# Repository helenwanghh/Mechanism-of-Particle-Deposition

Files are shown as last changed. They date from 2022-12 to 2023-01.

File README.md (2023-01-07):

# Mechanism-of-Particle-Deposition
Hello there!  Here is a project portfolio for my Senior Capstone Project (2021-2022)
This is a project provided by **Integrity Industrial Inkjet Integration** who needed a printing manufacturing process that can print on a wide range of surfaces. 

Please click the link to check out the Users Operation Instrution Video: 
Instruction Video for the Mechanism Design (https://www.youtube.com/embed/nuajtc9fk5U)
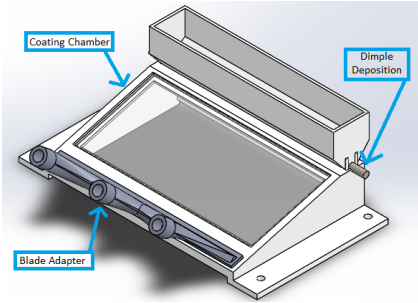
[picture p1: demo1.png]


- **Background**

The client currently has a method of layering adhesive and various powders on an inkjet conveyor that does not meet their standards.

- **Problem**

Provide proof of principle, using glitter as a substitute for various powders. The module is to be attached to a conveyor belt along with an Inkjet printer head that will dispense a uniform coating of glitter on an adhesive with a method to recover and reuse any additional glitter that is not used.

- **Benefits**

A fully functional module will prevent material waste and reduce cost while producing high quality/ high resolution prints for clients across several industries.

 **Client Requirements**

- Maintain clean workspace and ensure  minimal glitter escapes the box 
- Maximize glitter use to create less waste and reduce cost on materials
- A way to easily control device to stop or divert the glitter flow
- Must only remove excess glitter and not glitter that has been adhered
- Be able to do multiple colors of glitters and multiple layers of glute/glitters
- Must not exceed surface area of conveyer belt plate: 7.5'' x 7.5''

**Team picture captured at the Design Night at University of Vermont!! :) **
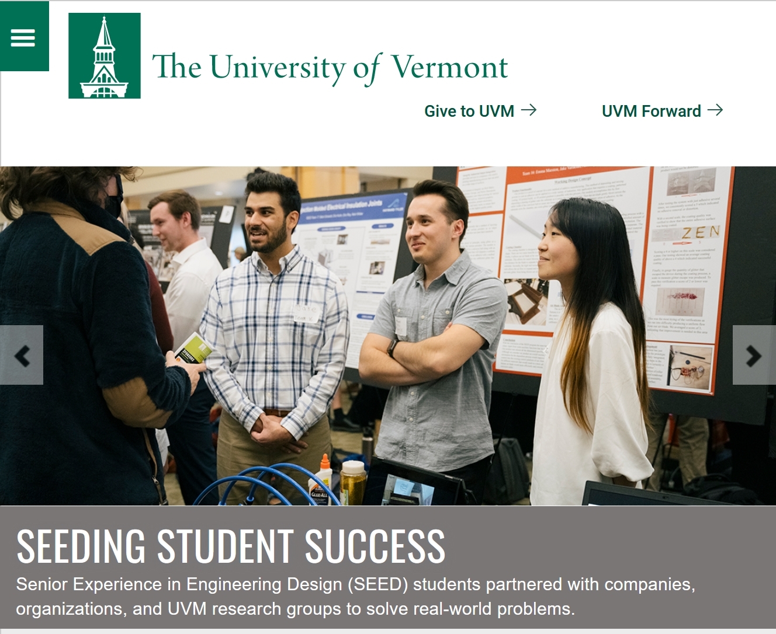
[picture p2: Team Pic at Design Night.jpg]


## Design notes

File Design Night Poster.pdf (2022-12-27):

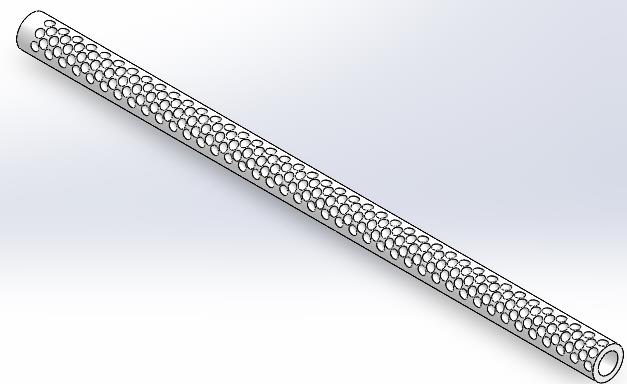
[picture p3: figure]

Background

The client currently has a method of layering adhesive and various powders on an inkjet conveyor that does not meet their standards.

Problem

Provide proof of principle, using glitter as a substitute for various powders. The module is to be attached to a conveyor belt along with an Inkjet printer head that will dispense a uniform coating of glitter on an adhesive with a method to recover and reuse any additional glitter that is not used.

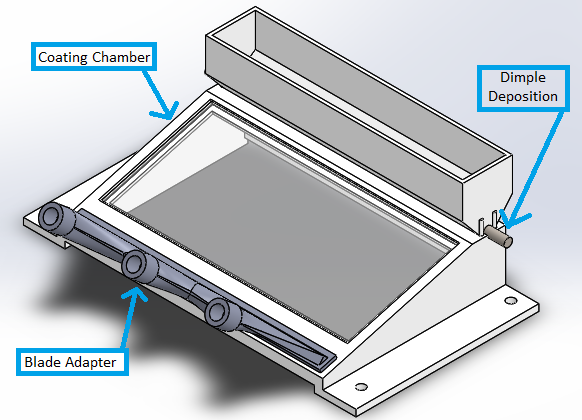
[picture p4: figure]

Benefits

A fully functional module will prevent material waste and reduce cost while producing high quality/ high resolution prints for clients across several industries.

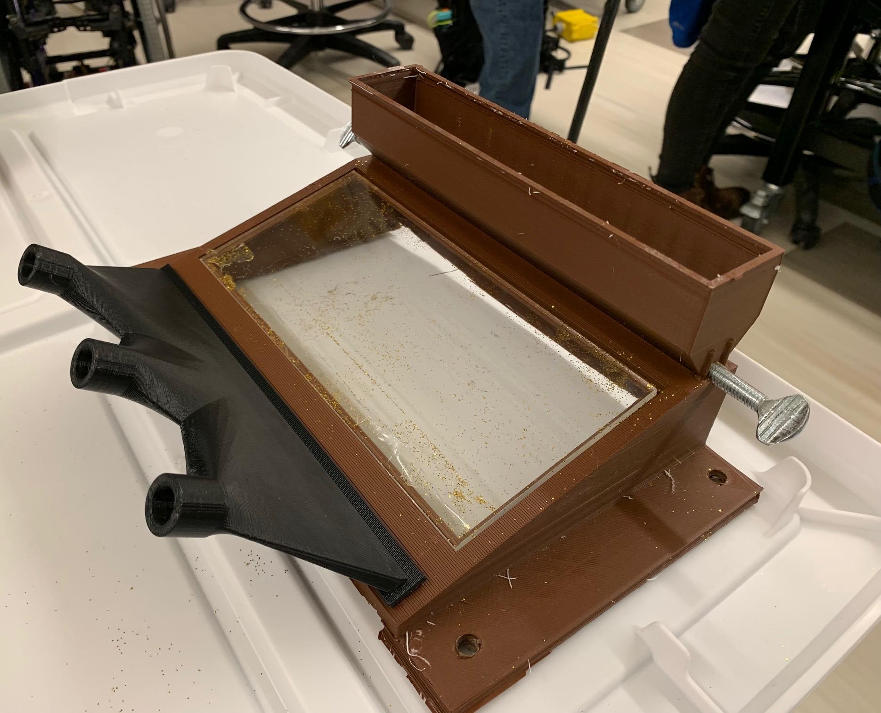
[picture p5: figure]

Client Requirements
- Maintain clean workspace and ensure minimal glitter escapes the box
- Maximize glitter use to create less waste and reduce cost on materials
- A way to easily control device to stop or divert the glitter flow
-Must only remove excess glitter and not glitter that has been adhered
- Be able to do multiple colors of glitters and multiple layers of glute/glitters
- Must not exceed surface area of conveyer belt plate: 7.5'' x 7.5''

Results
After refining the requirements stated by our client, specifications were developed, and a verification plan was prepared to document results.

In order to ensure image quality, a visual scale was created to quantify the amount of adhesive removed from the substrate. Scoring a 4 or higher on the scale resulted in a pass, ensuring the final product would not be distorted.

After testing the system with just adhesive several times, we consistently scored a 5 which indicated no adhesive removal or distortion.

With a second scale, the coating quality was verified to show that the entire adhesive surface was being coated.

Scoring a 4 or higher on this scale was considered a pass. Our testing showed an average coating quality of above a 4 which indicated successful coating.

Finally, to gauge the quantity of glitter that escaped the device during the coating process, a scale to measure glitter escape was produced. To pass this verification a score of 2 or lower was required.

This was the most trying of the verifications as we ran into difficulty producing a uniform flow from our air blade. We averaged a score of 3, indicating that improvement is needed in this area

## Team 16: Emma Marston, Jake Varakian, Anthony Vieriu, Helen Wang

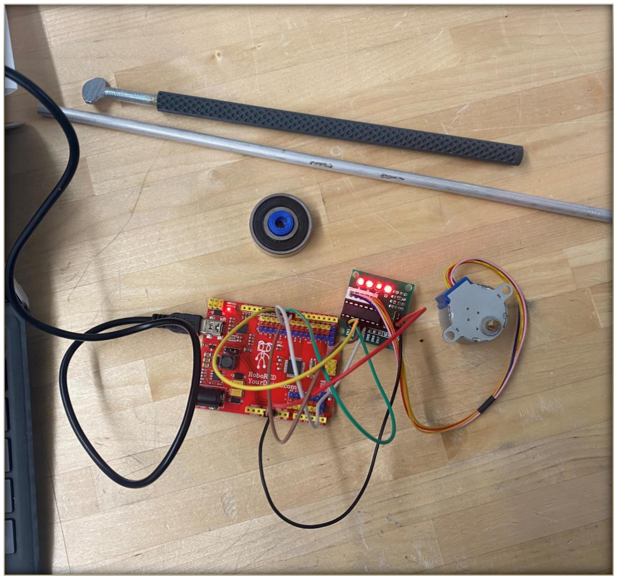
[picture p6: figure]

Conclusion
With the conclusion of the SEED program the team has delivered a product that performs all the main functions required by the client. Apart from some auxiliary functions that the team wanted to include, we consider this project a success.
Our product met almost all the determined specifications with a pass rate of 86%.
Although we consider our product an overall success, we have several suggestions for improving this design. Firstly, better automation for the deposition process would improve the user experience for the conveyor technician. Integrating motor control into the existing control platform of our client would improve usability. Additionally, if the deposition was adjustable for different materials that would result in a more adaptable product for varied applications. Finally, a more uniform and thinner air blade would more efficiently and consistently clear glitter from the substrate and prevent material escape from the conveyor outlet.

Acknowledgments
- Mentor: Jeffery Marshall
- Instructors: Dustin Rand, Ken Burkman
- UVM Fablab

Integrity Industrial Inkjet Integration provides services to companies who need a printing manufacturing process that can print on a wide range of surfaces.

Our contacts at Integrity are Rich Baker, Mackinley George, and Myles Duncanson. Their company uses Inkjet printing for various applications such as, industrial graphics, material deposition, printed electronics, bioprinting, and many more, to ensure their clients receive the highest quality prints.

Coating Chamber
The coating chamber is designed to resemble a wedge shape. There are two main benefits to this geometry. Firstly, it allows our air blade to be very close to the substrate. This allows for easier blowing of glitter due to less distance for the blade to separate before hitting the substrate. Secondly, the high end towards the conveyor inlet allows the air flow to expand and slow down, this prevents glitter from being blown out of the box.

Dimple Deposition
The roller covers the entire width of the conveyor belt to begin the coating process with a shower of glitter. The dimple design on the surface allows it to collect a controlled amount of glitter from the hopper and deposit a dusting instead of a clump with each revolution. The dusting makes coating and mixing much easier as clumps would be difficult to separate. The roller slides onto a ¼ inch metal shaft where it is secured with glue. The additional material that sticks out is used to hand-turn the roller. The team used this for testing to control the deposition, additionally, this is useful for breaking jams in the hopper/roller.

Product Functionality
Our product is a proof of concept for a new method of additive manufacturing. This method of depositing and mixing powder to coat an adhesive can be applied to a wide variety of industries. Any application that requires a coating, patterned coating, 3D printed build, or 3D printed gradient is possible with this process. Our module accomplishes this by first depositing a dusting of glitter onto the substrate as it enters the coating chamber. Then the air blade gently blows across the entire width of the conveyor belt to cause any loose glitter to tumble backwards and coat empty areas of adhesive. As the substrate exits the chamber, any extra glitter continues to tumble backwards and can be used for the next coating

## Working Design Concept

Air Blade Adaptor
The air blade adaptor takes the flow through the air pump tubing and flattens it out to resemble more of a blade. This allows us to clear glitter off the entire width of the conveyor belt. By spreading the flow across a larger area, we also reduced the strength of the flow, allowing for more precise calibration to ensure we aren’t blowing glitter out of the chamber.

Continuing Development
Automated deposition has just recently been added to the prototype. While this is not yet fully integrated, we have begun taking steps in the right direction and this is certainly a solid foundation for further development. The addition of roller bearings has also reduced rotational friction in the deposition assembly, improving the process further.

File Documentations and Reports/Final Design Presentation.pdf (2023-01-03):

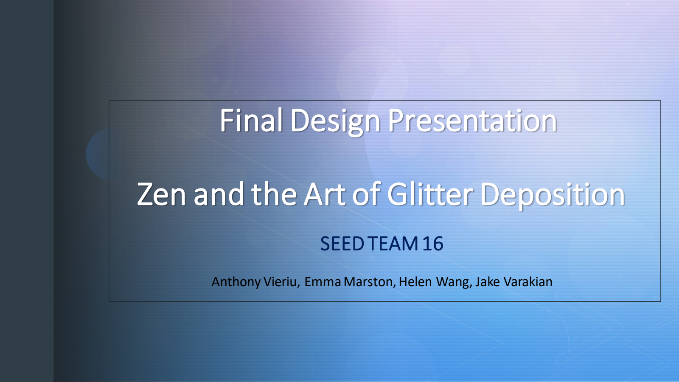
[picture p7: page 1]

z

z

# Final Design Presentation

# Zen and the Art of Glitter Deposition

# SEED TEAM 16

### Anthony Vieriu, Emma Marston, Helen Wang, Jake Varakian

z | Introduction
| Our Client

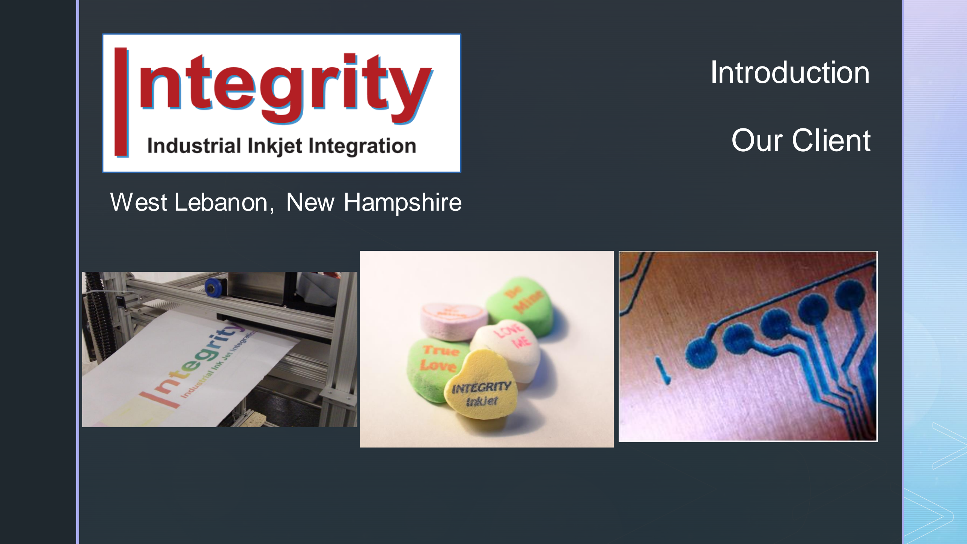
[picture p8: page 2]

## West Lebanon, New Hampshire

# The Team

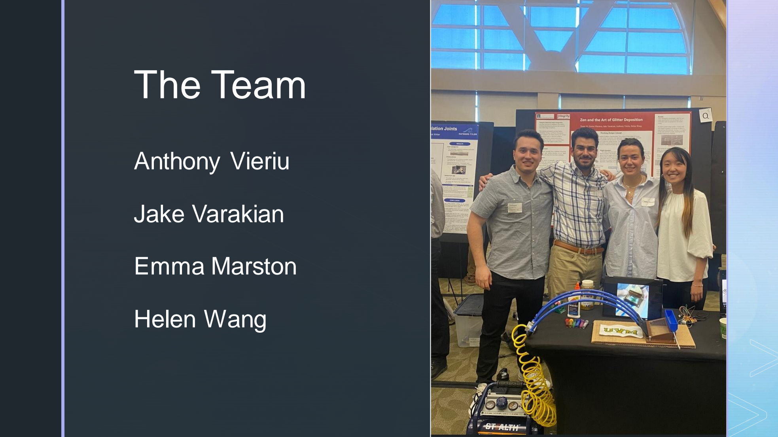
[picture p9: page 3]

z

z

## Anthony Vieriu

## Jake Varakian

## Emma Marston

## Helen Wang

z

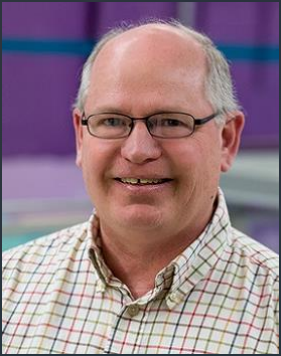
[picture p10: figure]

# Our Mentor

# Dr. Marshall

z

# Problem Statement

Develop a module to be attached to an inkjet conveyor that will dispense a uniform coating of glitter on an adhesive with a way to recover excess glitter.

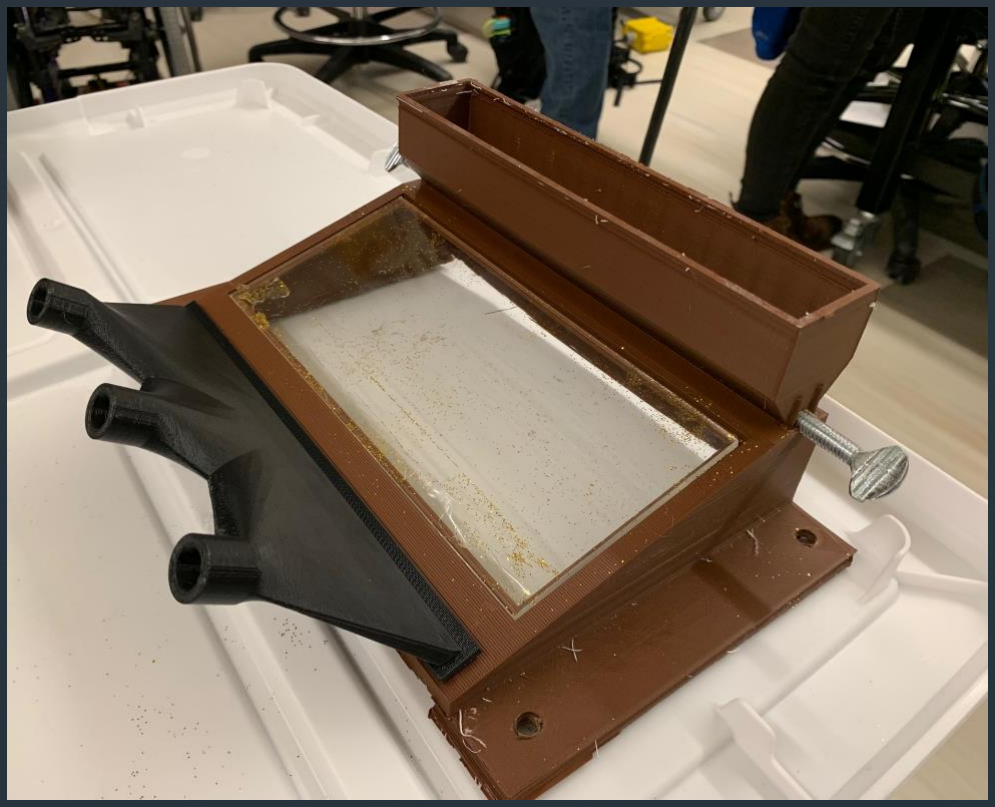
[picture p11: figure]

z

# Customer Requirements

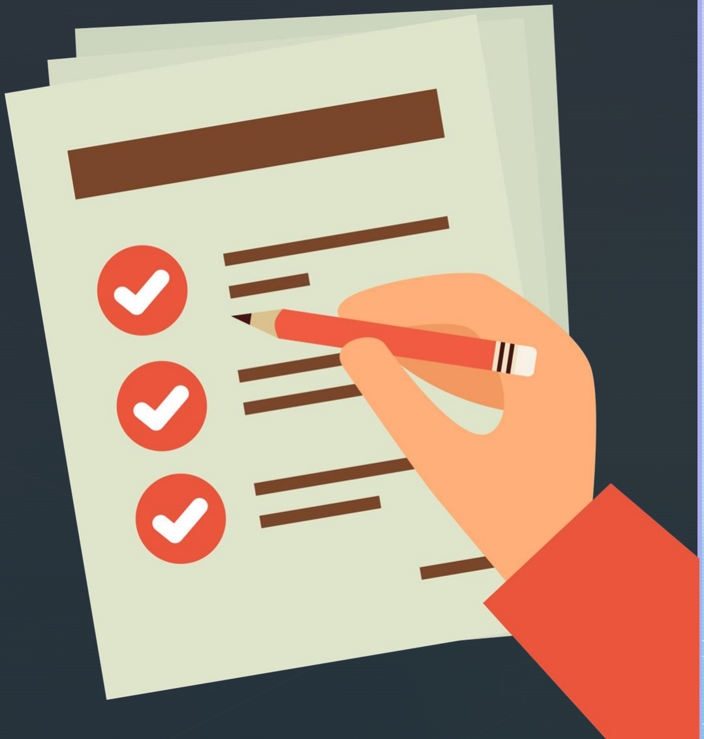
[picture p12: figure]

1. Clean workspace
2. Minimal waste
3. Easily controlled
4. Remove only excess glitter
5. Multiple colors
6. Fit within given parameters

# Each Part Serves A Specific Function

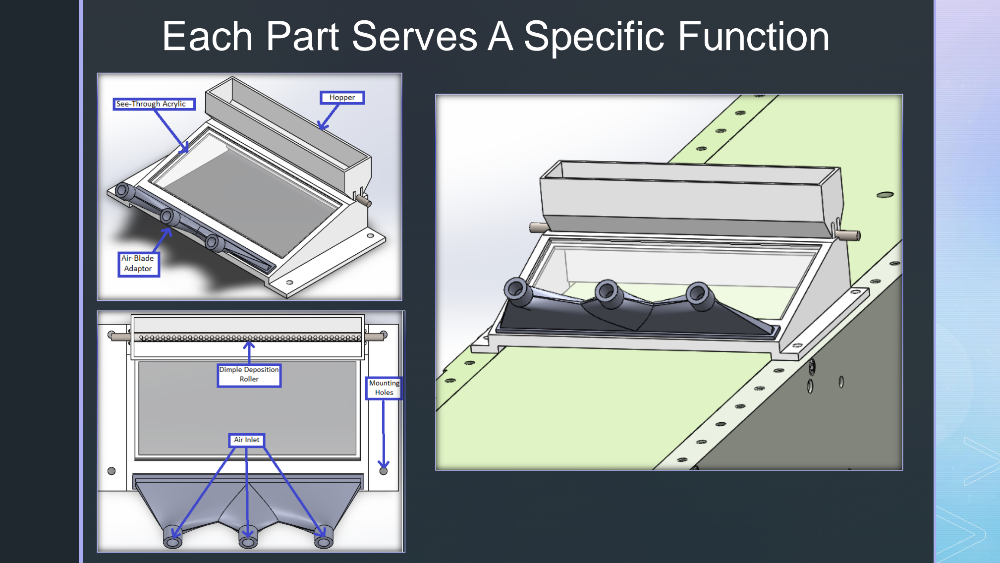
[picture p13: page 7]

z

z

z

# Easily Controllable Deposition

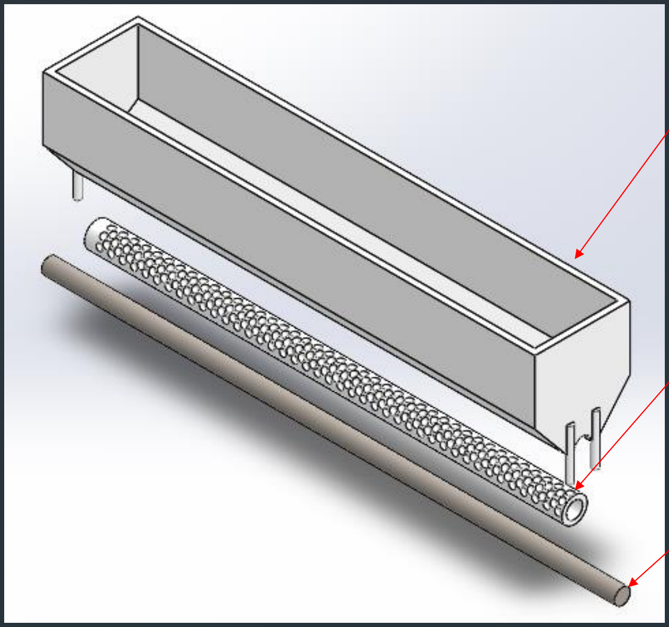
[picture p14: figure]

Multiple to coatings prepared at once

Rotation easily controlled

Dusting not clumps

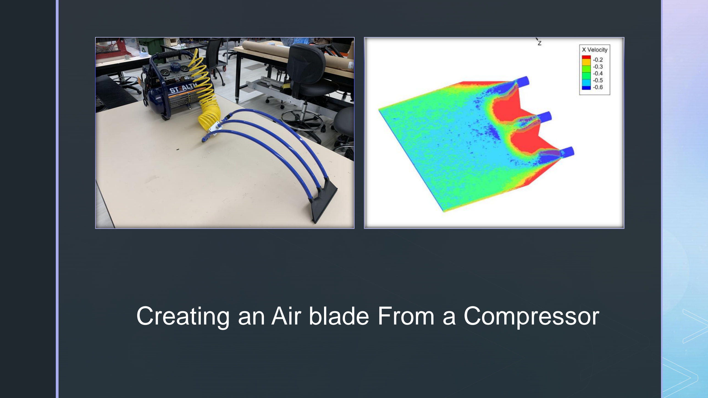
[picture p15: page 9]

z

z

# Creating an Air blade From a Compressor

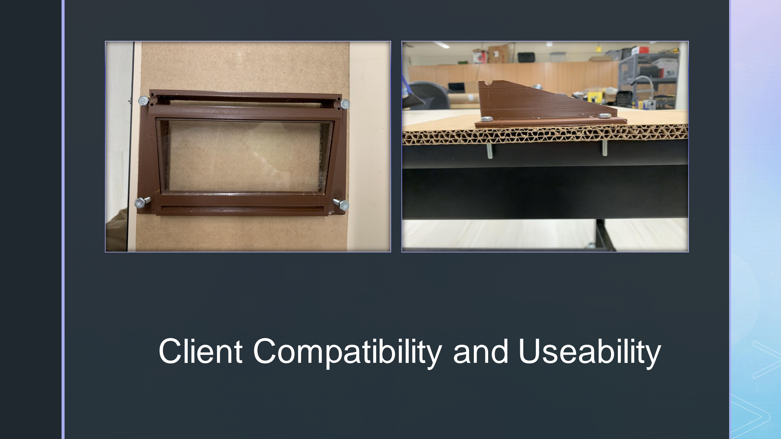
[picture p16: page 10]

z

z

# Client Compatibility and Useability

# Organizing the Solution to the Problem

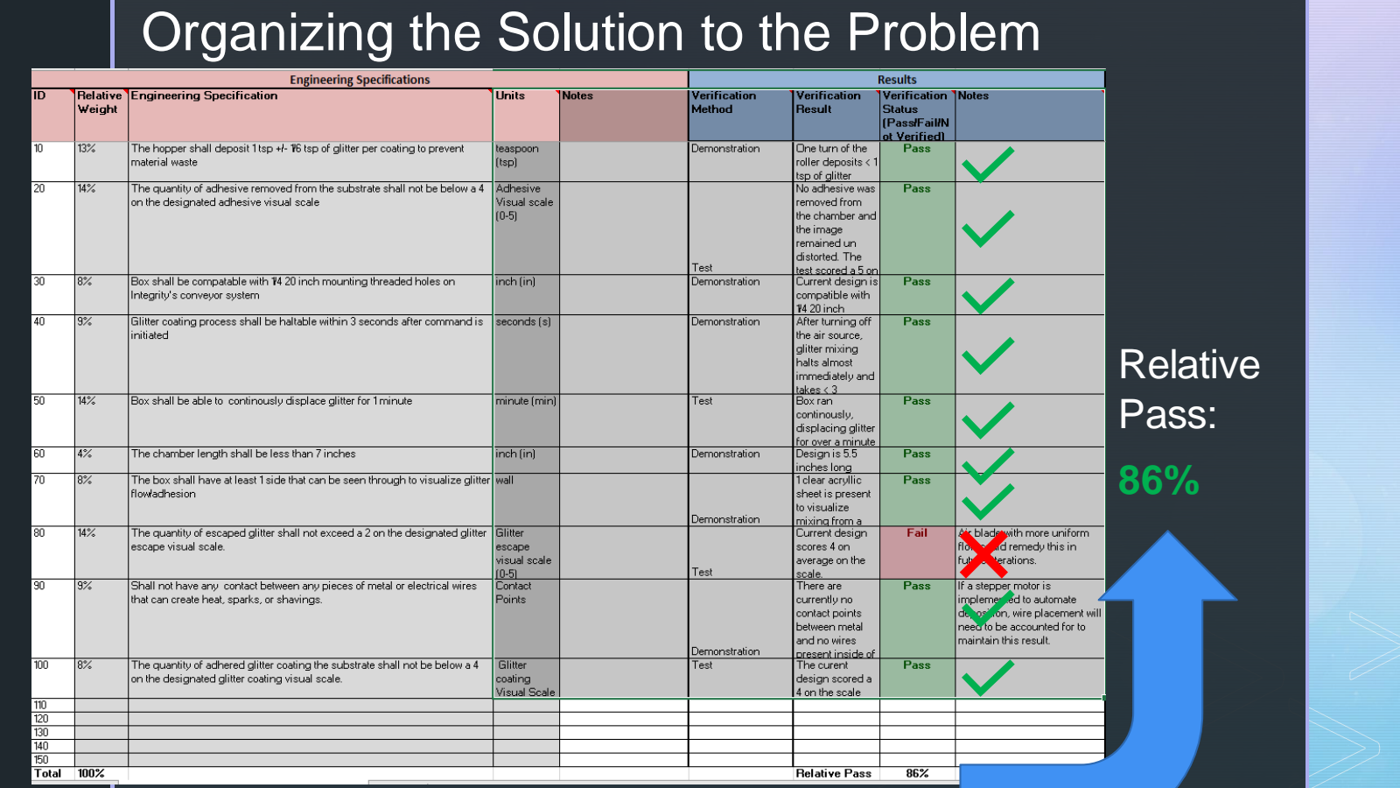
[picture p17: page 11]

z

## Relative Pass:

86%

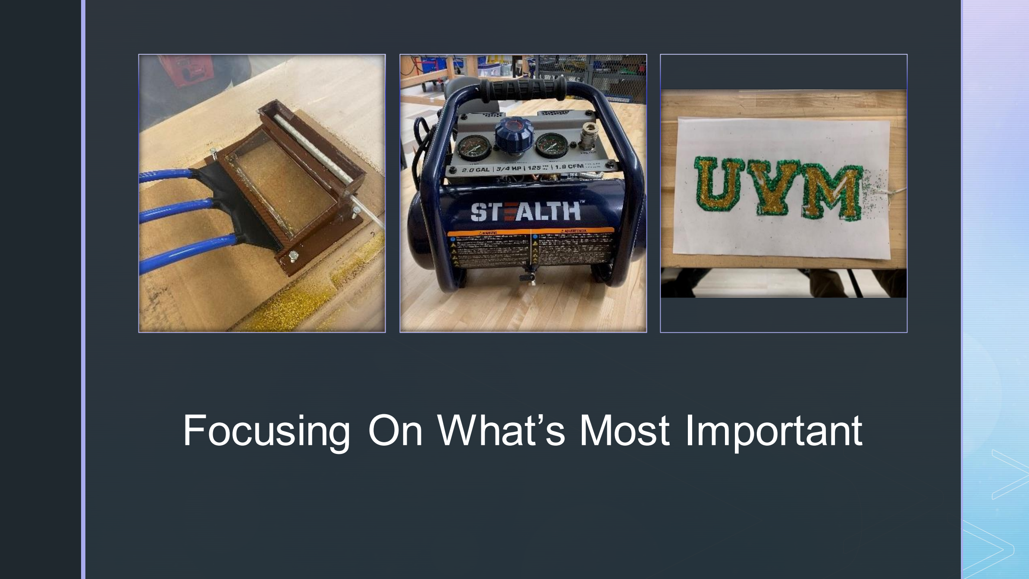
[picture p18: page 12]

z

z

# Focusing On What’s Most Important

# z Containing The Particles: ID 80

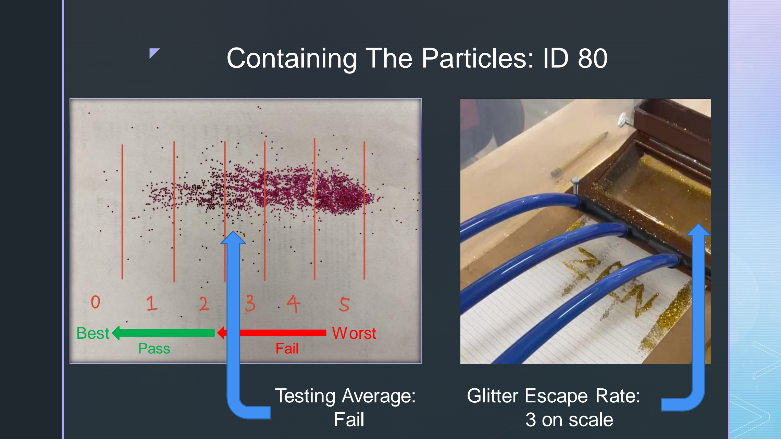
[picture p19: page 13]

Best | Worst

## Testing Average: Fail

## Glitter Escape Rate: 3 on scale

Pass | Fail

# z Nonstop Printing Process: ID 50

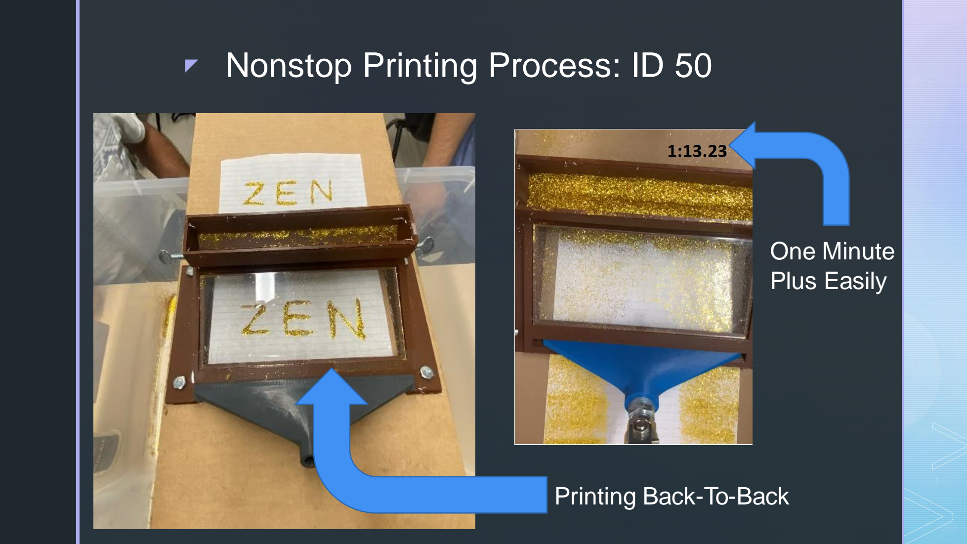
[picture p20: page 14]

## One Minute Plus Easily

## Printing Back-To-Back

# Open issues (continuing development)

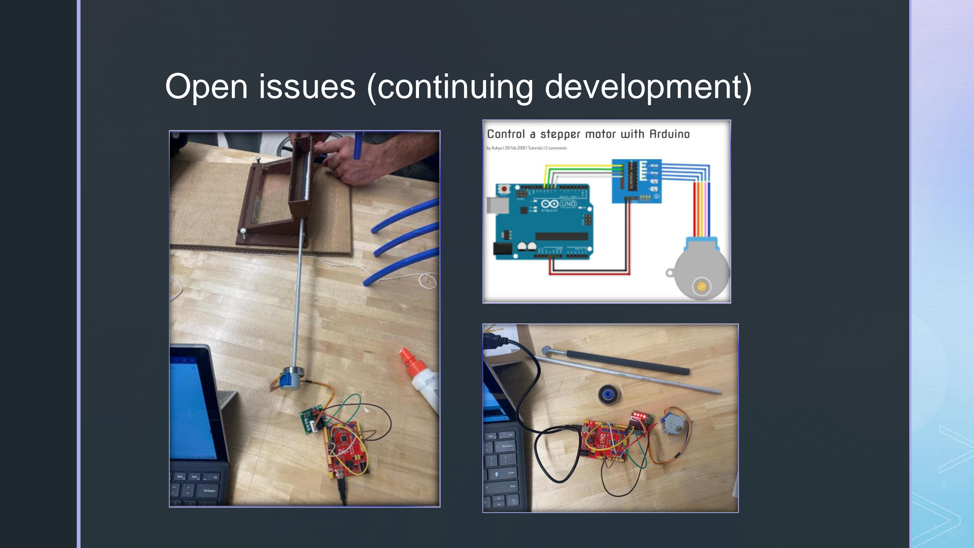
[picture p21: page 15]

z

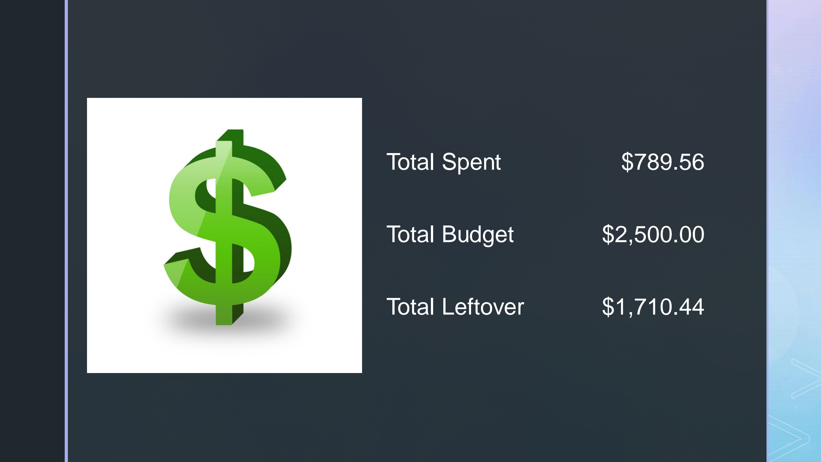
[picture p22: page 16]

z

z

Total Spent | $789.56
Total Budget | $2,500.00
Total Leftover | $1,710.44

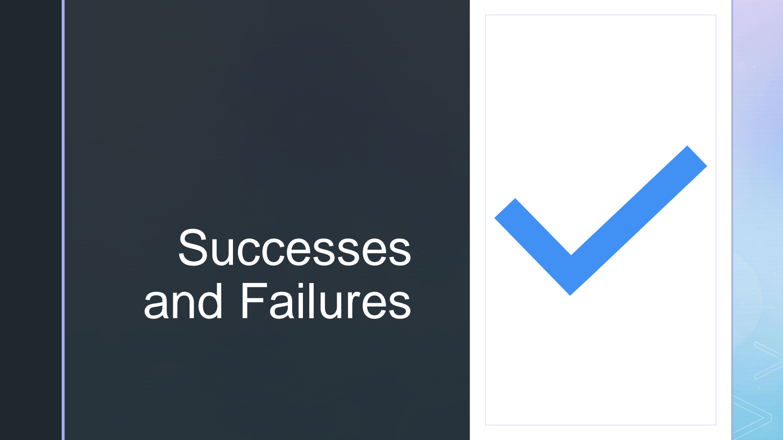
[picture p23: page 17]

z

z

# Successes and Failures

z

# Implementing Feedback Into Design Iteration

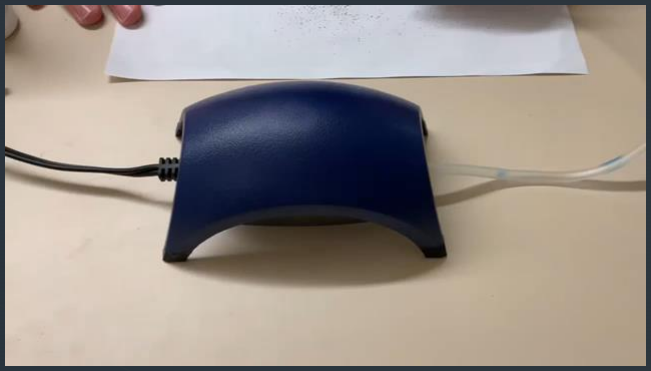
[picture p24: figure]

Feedback from Sprint 5

- Aquarium tubing that releases bubbles (can precisely speed up or down the air with valves)

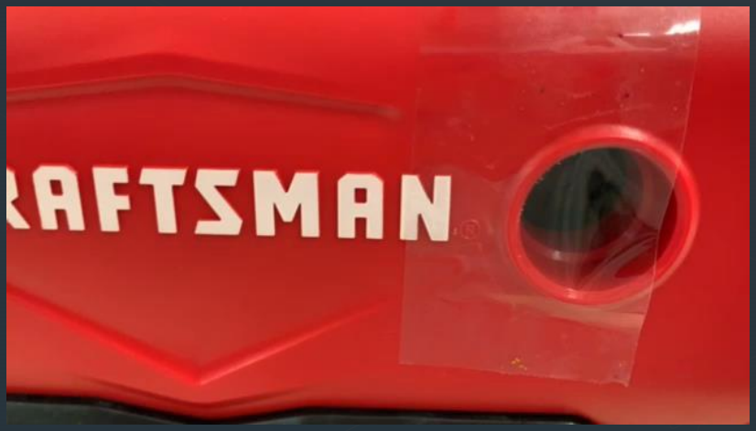
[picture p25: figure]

- Consider flute (manifold tube with multiple ports)
- Can also pinch the tubes and control the pressure

Sprint 6 Testing

# Client Satisfaction

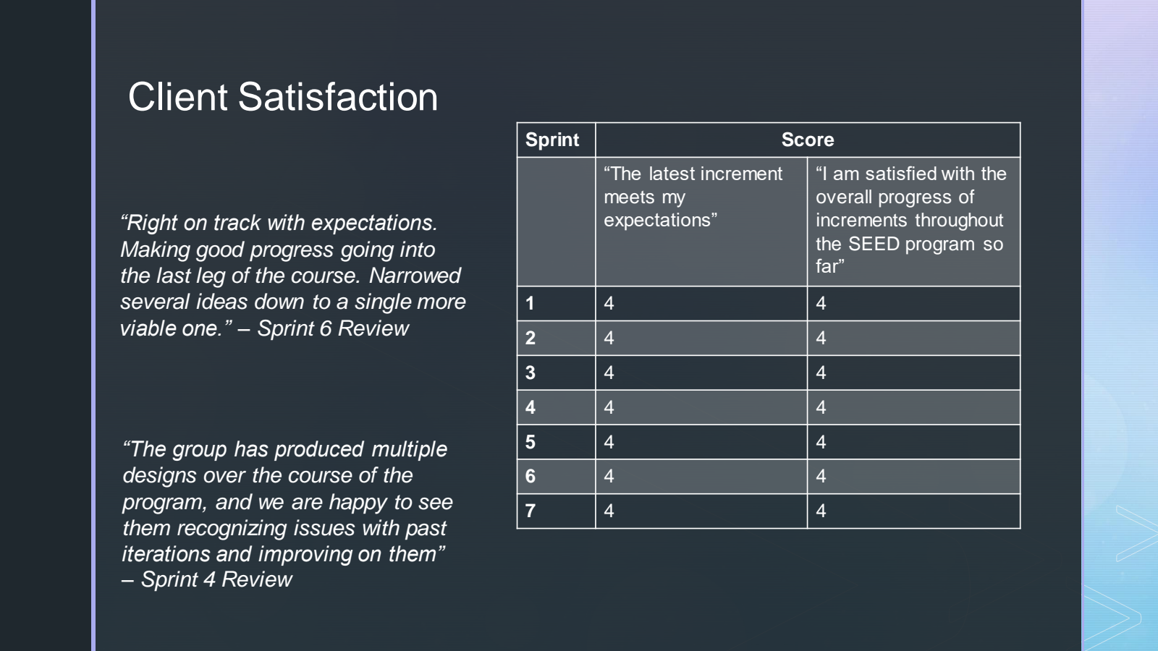
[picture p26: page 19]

z

z

Sprint | Score
| “The latest increment meets my expectations” | “I am satisfied with the overall progress of increments throughout the far” | SEED program so
1 | 4 | 4
2 | 4 | 4
3 | 4 | 4
4 | 4 | 4
5 | 4 | 4
6 | 4 | 4
7 | 4 | 4

“Right on track with expectations. Making good progress going into the last leg of the course. Narrowed several ideas down to a single more viable one.” – Sprint 6 Review

“The group has produced multiple designs over the course of the program, and we are happy to see them recognizing issues with past iterations and improving on them” – Sprint 4 Review

# Lessons Learned

# 1. prototyping tolerance issues


z

z

# Lessons Learned

# 2. communication between teammates and clients


z

z

Final Design

First Design

z

z | Thank You

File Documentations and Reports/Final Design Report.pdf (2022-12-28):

# Final Design Report

_____________________________________________________________________________________

Project 16 – Zen and The Art of Glitter Deposition

Team Members:
Jake Varakian
Emma Marston
Helen Wang
Anthony Vieriu
Date | Revision | Release Notes
5/6/2022 | 01 | Initial Release

SEED Team 16 | Final Design Report | 1

## Table of Contents

1 | Abstract
| 3
2 | Problem Statement
| 3
3 | Requirements
| 3
4 | Work Design Concept
| 5
5 | Analyses
| 9
5.1 | CFD Analysis of Two and Three Inlet Air Blade Adaptor Designs
| 9
5.2 | Mathematical analysis of Dimple Design and Glitter Deposition Volume
| 11
5.3 | Coefficient of friction comparison
| 8
5.4 | Optimizing wind speed calculations
| 14
6 | Engineering Specifications
| 18
7 | Conclusion
| 19
7.1 | Successes and Failures
| 11
7.2 | Overall Satisfaction
| 11
7.3 | Recommendations for Future Development
| 11
8 | Impact Statement
| 21
9 | Lessons Learned
| 21
10 | Project Retrospective
| 22
11 | Product Review
| 23

12 | Budget Review
| 24
13 | Citations
| 15

### 1 Abstract

In the Fall of 2021, the team set out to create a module that would efficiently and completely coat adhesive with glitter while reusing any non-adhered particles. The current design is a wedge-shaped chamber with mounting holes on either side to attach to the conveyor belt located at Integrity Industrial Inkjet Integration. The chamber makes use of a hopper and roller deposition method to deposit a dusting of glitter onto adhesive patterns entering the chamber. Then at the exit of the chamber, a blade of air causes loose glitter that would exit the chamber to tumble backwards. This tumbling motion prevents glitter from escaping while also continuing to coat the adhesive further back in the chamber. After working on this design for two semesters, the team developed a product that accomplished all the goals set out in Fall 2021 apart from preventing glitter escape from the chamber. The next steps for this project would be to continue development of the air blade attachment to create a more uniform blade of air, thus improving the clearing of the conveyor belt. Additionally, implementing an automated deposition system would greatly improve the real-world functionality of the module.

### 2 Problem Statement

Our client is Integrity Industrial Inkjet Integration, a company that uses inkjet technology for various applications across a wide range of industries. The function of interest for this project is the application of powders to a substrate. This is done by using inkjet printer heads to spray adhesive in a programmable pattern and sending the patterns through a continuously depositing curtain of powder across the width of a conveyor belt. The adhesive is then cured with a UV light and more layers of adhesive and powder may be added. The problem with this current method is that material use is extremely high with no recovery method to reuse the material that isn’t adhered to the substrate.

The client requested proof of concept for a module that would coat a layer of adhesive with glitter and reuse any glitter that is not adhered. This module would be used in conjunction with their current Inkjet and UV curing setup to stack multiple layers of powder and adhesive while reducing material waste. A fully functional product would reduce material waste and save money on manufacturing across a plethora of industries. Additionally, due to the conveyor compatibility, the module could be used in high-speed manufacturing to continuously coat items without the need for batch coatings.

The main qualities of a successful module are to ensure the adhesive is completely coated with no deformation of the desired pattern. It should also be able to remove excess glitter and utilize it for subsequent coatings with minimal glitter escaping from the chamber. A product that performs these main functions would be considered a success.

### 3 Requirements

The complete list of requirements and how they are weighted by potential customers is found below. The three customers identified for this table are: Integrity, Integrity’s Customers, and the conveyor technicians that would be working with the module. Each of the requirements was given a score to represent its importance to each customer. Additionally, each customer was given a different number of points to represent the weight of their opinion.

Table 1: Customer Requirements

Customers | | Requirements
Integrity | Integrity’s Customers | Conveyor Technicians | Category | Requirement
10 | 7 | - | Functionality | Remove excess glitter without removing adhered particles
13 | 10 | - | | Remove excess glitter without removing any adhesive
15 | 10 | - | | Glitter covers the adhesive efficiently
9 | 3 | 10 | | Ensure minimal glitter escapes the box
6 | - | 5 | | Box must be securely mountable to Integrity’s conveyor system
5 | - | - | | Must not take up too much space on Integrity’s conveyor
5 | 5 | 10 | | Operates for long durations reliably
13 | 7 | | | Glitter must be randomly and evenly distributed across adhesive
8 | 5 | 10 | Safety | Box must have zero risk for particle ignition
8 | 3 | 10 | | A way to easily control device to stop or divert the glitter flow
8 | - | 5 | Aesthetic | Box shall have a way to clearly observe particle flow within it

The three highest scored requirements for each client have been bolded in the above table. For Integrity and their clients, the top three requirements match as their priorities are very similar. For the conveyor technician, high level requirements focus on potential hazards when operating the module and mitigating risk.

The highest-level requirement for both Integrity and their clients was, “Glitter covers the adhesive efficiently,” this is a fundamental function of the module. The main purpose of the glitter module is to reduce material waste, if this is not accomplished then the main improvements over the current method have not been completed. The second high-level requirement is, “removes excess glitter without removing any adhesive,” this is an especially important requirement as maintaining the image quality is crucial. If the image exiting the module is different from the one desired by the client, then the box has failed. The final high-level requirement for integrity and their clients is, “glitter must be
randomly and evenly distributed across the adhesive”. This requirement is important as it ensures that the entire design is coated without any bias towards a specific area of the conveyor belt. This guarantees that any design would be coated with shape not being a factor.

The three highest level requirements for the conveyor belt technician all scored the same and center around maintaining the safety of the technician. The first is “ensure minimal glitter escapes the box”. This requirement is important as powder escaping into a manufacturing line could cause issues with the other machinery present resulting in a shutdown of the entire conveyor belt. Also, depending on the powder, inhalation could be dangerous as well. The second high-level requirement is that “the box must have zero risk for particle ignition.” Due to the flammability of some powders, having any ignition risk combined with mixing within the chamber could be extremely dangerous. The final high-level requirement is “a way to easily control device to stop or divert glitter flow”. In the case of any sort of error on the conveyor belt, it is important to have a way to stop the deposition of glitter quickly and safely. This could prevent issues on the manufacturing line from getting worse as well as prevent unnecessary material waste.

### 4 Work Design Concept

### 4.1 Functionality

This product is a proof of concept for a new method of additive manufacturing. This method of depositing and mixing powder to coat an adhesive can be applied to a wide variety of industries. Any application that requires coating, patterned coating, 3D printed build, or 3D printed gradient is possible with this process. This module accomplishes this by first depositing a dusting of particles onto an adhesive coated substrate as it enters the coating chamber. Then the air blade gently blows across the entire width of the conveyor belt to cause any loose particles that never landed on and/or aren't touching the adhesive to tumble backwards and coat the emptier areas of the adhesive. As the substrate exits the chamber, any extra glitter continues to tumble backwards remaining inside the chamber and can be used for the next coating

### 4.2 Coating Chamber

To accurately convey the functionality of the coating chamber, each part will be described in such a way that allows the reader to understand what each section of the part is for. First starting with the main chamber. It has two 7.5-inch openings on either side for the substrate to come into and out of the chamber on Integrity's conveyor belt system. On the top there is a clear acrylic sheet which allows the operator to see the coating process inside the chamber as it is running, and an opening for particle introduction into the chamber. Also, on each side there are two 1/4 20-inch mounting holes spaced 4.5 inches apart to mount onto Integrity’s conveyor belt system. Overall, the coating chamber is designed to resemble a wedge shape. There are two main benefits to this geometry that allow the wedge to perform its job effectively. Firstly, the conveyor outlet side of the chamber is low and close to the substrate, this allows the air coming in through the air blade adapter to blow as close to the substrate as possible. Glitter can easily be blown by the air due to this small distance between the blade and the substrate, allowing the air speed to stay as close to a minimum as possible ensuring the particles don't blow too far, and out of the conveyor inlet. Secondly, the high end towards the conveyor inlet aside allows the air flow to expand and slow down as it travels down the length of the inside of the chamber, this will further prevent glitter from being blown out of the conveyor inlet. The following image, figure 1 is a computer-generated image of the full wedge assembly showcasing all the parts.


Figure 1: System Overview

### 4.3 Air Blade Adaptor

The air blade adaptor is a 7.5-inch-wide air control mechanism that takes in airflow from three equidistant inlets which are each connected to a tube that connects to an air compressor. The purpose of the air blade adapter is to transform the shape of the air coming in from the pump to resemble a flat 7.5-inch-wide blade. This shape of airflow will be used to gently clear glitter off the entire width of the conveyor belt. As the flow spreads across a larger area the speed of the flow is naturally reduced along the length of the adapter, allowing for more precise calibration to ensure particles aren’t blowing out of the chamber. Additionally, the adaptor causes unadhered particles to tumble backwards, which assists in the coating of any remaining adhesive.


Figure 2: Air Blade Adaptor

### 4.4 Dimple Deposition

The dimple roller is a 7.5-inch-wide cylinder that covers the entire width of the conveyor belt. The roller is the beginning of the coating process, showering the substrate with a dusting of particles. The dimple design on the surface allows the roller to collect a controlled quantity of particles from the hopper and drop them into the chamber. The dimples also ensure that no clumping takes place with each revolution. The dusting makes coating and mixing easier because clumps of particles would be more difficult to separate from one another and may not blow through the system very well. The roller slides onto a ¼ inch metal shaft to provide rigidity and support along the length of the cylinder, securing everything in place with glue. The additional material that sticks out is used to hand-turn the roller. The team used this hand turning method for testing/controlling the deposition, but additionally would be useful for breaking jams in the hopper/roller assembly. While the hand deposition was useful in the development phase, automation of this process is a key part of the future steps for this design.


Figure 3: Dimple Deposition Roller

### 4.5 Hopper

The hopper subassembly is a 7.5-inch-long chamber to align with the dimensions of conveyor belt and dimple deposition and chamber assembly. The legs at the bottom of the hopper are the attachment points for connecting with the chamber. The hopper design on the top allows the glitter to be added into the product. The opening at the bottom is connected to the dimple deposition cylinder, the dimensions of the hopper opening’s length and width align with the dimple roller length and diameter. The alignment with the dimple deposition is critical and was one of the challenges during the design process because of the potential of glitter escaping. Geometry tolerancing and dimensioning are a critical perspective of this design, which showed the importance of this part and the parts above.


Figure 4: Hopper

### 4.6 Visual Scale

All the testing results are measured by the visual scale created by the team. The visual scale on the left verifies that glitter entering the system is not blown out of the module into the surrounding area. This will be done by running the system as intended and using a visual scale to score the amount of escaped glitter based on an acceptable range. The visual on the right verifies that the method for removing glitter does not also remove the glitter that has landed on the adhesive. This will be done by running the system with wet glue that has been pre-coated with glitter and comparing the number of displaced particles to the pre-determined visual scale.


Figure 5: visual scale of glitter escaping rate | Figure6: visual scale of glitter coating rate

### 4.7 Design Overview

The design contains 4 subassemblies described above: air blade adaptor, dimple deposition, hopper, and the chamber. They were prototyped by 3D printing and ABS material. The design demonstrates the concept for a new method of additive manufacturing. Applications include decorative coating and 3D particle printing are possible to be applied with this design.


Figure 7: Product Prototype | Figure 8: UVM logo printed by glitter box design

### 5 Analyses

### 5.1 CFD Analysis of Two and Three Inlet Air Blade Adaptor Designs

Coming into the second semester of the SEED program, the team began experimenting with the use of an air blade adaptor to convert the pipe flow from the air source into a flat blade of air. This would make the uniform removal of glitter from the substrate much easier by spreading the airflow across the entire width of the conveyor belt. The first iteration of the air blade adaptor had a single inlet and a single outlet. While this design showed some promise for the concept of the adaptor, it failed to clear the entire width of the conveyor belt. The problem was that the flow from the pump was not expanding to fill the entire rectangular outlet. There was significantly more flow towards the center of the outlet and the edges of the conveyor belt remained uncleared. To remedy this problem, new versions of the adaptor with multiple air inlets were developed. The hope was that the multiple inlet designs would promote a more uniform blade of air by reducing the area that each stream had to expand across.

Before printing the new versions with two and three inlets, CFD was used to predict how each might perform and determine how they might be improved. ANSYS/Fluent was used to run the CFD, these programs make use of the continuity equation and the Navier-Stokes equation to solve for basic flow characteristics.
| Continuity: ∂ρ ∂t + ∇ ⋅ (ρ ⋅ v) = 0

Navier − Stokes: ρ (

| dV dt + v ⋅ ∇v) = −∇p + μ∇ 2v + f

The SolidWorks models of each adaptor were exported into ANSYS Workbench where a volume extraction was used to mesh the space where air would be flowing. In addition to the interior of the adaptor, space directly out of the outlet was also meshed to see how the flow spread out once leaving the adaptor. This interior mesh was generated using a sphere of influence method centered about the origin of the SolidWorks model, each element was given a size of .001 m. This method was used for both versions and resulted in a mesh of 467784 finite volumes for the 2-inlet version and 472308 finite volumes for the 3-inlet version. The default generated mesh for the solid blade adaptor was kept as there would be no flow through the solid walls. Inlet and outlet boundary conditions were specified for each version and the finished meshes were exported to Fluent where the simulations would be run.


Figure 9 and 10: Interior Meshes for each version

Once in Fluent, the simulation parameters were set. A pressure-based steady-state simulation was used with air as the working fluid. The air was given the values of ρ = 1.225 kg
m³

and μ = 1.225 kg
m⋅s

,
it was assumed that the density and viscosity of the air would remain constant. For each version, a total velocity magnitude across all inlets of 4 m
s

normal to the boundary was used. This is to replicate the single flow being split into multiple paths. All pressure outlets were given a gauge pressure equal to atmospheric pressure, 101325 Pa.

The parameter of interest for this analysis was the x-velocity contour. Looking at the x-velocity contour would allow the group to visualize the distribution of flow exiting the blade adaptor. Ideal results would have a constant velocity across the entire exit of the adaptor indicating a uniform flow. Upon looking at the results below, there are still significant gaps in the contour for the two-inlet adaptor. While this design is still an improvement on the single-inlet adaptor, there is now a small gap at the center in addition to the small gaps along the edges. The areas that would be theoretically cleared by the two-inlet adaptor have a velocity magnitude of about 0.55 m
s

Upon looking at the results from the three-inlet adaptor, we see a more uniform flow across the exit. While there is some noticeable speckling of the velocity, this iteration covers more of the exit with more consistent flow. The average outlet velocity for the three-inlet adaptor is around 0.5 m
s

. This lower
exit velocity makes sense as the mixing of all three flows would result in some velocity losses.


Figure 11: Two-Inlet X-Velocity Contour Figure 12: Three-Inlet X-Velocity Contour

When looking at these results it is important to note that, to better see the flow at the edge of the mesh, the low end of the scale was brought up. Because of this, much of the flow close to the inlet is displayed as having a velocity of 0.6 m
s

when it is actually higher. This is especially noticeable for the two-inlet version.

Using these results, the team concluded that the three-inlet design would perform the best out of the three designs. Both the two and three-inlet designs were 3D printed in a batch at the same time. Experimental tests confirmed the computational results, and the three-inlet adaptor was implemented into the final product where it greatly improved upon the single inlet design.

### 5.2 Mathematical analysis of Dimple Design and Glitter Deposition Volume

Dimple deposition is one of the innovative designs of the project. The roller is a long cylindrical shaft with dimples covered on ½ size of the surface area. The team was inspired by the mechanism of gumball machine at the very beginning and designed a cylindrical shaft with an extrude cut on one side of the surface. There was a problem with this design because it caused depositing in clumps and made it difficult to mix glitter. Later throughout the semester, the team was inspired by the idea of dimples on the golf ball, which would scoop smaller amount of glitter with each dimple, therefore, the design was upgraded by having dimples on the surface, and this change was designed to “dust” instead of dropping clumps. The roller covers the entire width of the conveyor belt to begin the coating process with a shower of glitter. The dimple design on the surface allows it to collect a controlled amount of glitter from the hopper and deposit a dusting with each revolution.

To analyze this dimple deposition functionality, it is important to have precise calculations of the amount of glitter deposited in one rotation so the user would have a clear idea on material quantity of product impact. By comparing the result of the dimple deposition volume with one of the engineering specifications that “the hopper shall deposit 1 tsp+/- 1/6 tsp of glitter per coating to prevent material waste”, the mathematical analysis will show the deposition result of the dimple deposition design.

-Mathematics equations & calculations:

- The volume of a teaspoon: Vt = 0.301 in^3
- Volume of a deposition cylinder with no openings: Vo = 0.56 in^3
- Volume of a deposition cylinder with dimples: Vd = 0.46 in^3
- Volume of dimples: V= Vo-Vd = 0.56 in^3 – 0.46 in^3 = 0.1 in^3
- How many teaspoon is the volume including overfill:

(0.1in^3 / 0.301 in^3)*(1 teaspoon) = 0.332 teaspoon

-The data of volumes above were acquired from solidworks function “mass property”.


Figure 13: Dimple Deposition | Figure 14: Cylindrical shaft without dimples

Calculations prove that the long dimple deposition takes less than one teaspoon of glitter to the system per rotation. Multiple rotations will yield the necessary amount of glitter for each individual coating assignment. Mathematical analysis proves that the goal of dimple deposition design is not only having a precise design on glitter deposition, but also proves that the design doesn’t waste glitter while printing. It is significant to make sure the glitter deposition is precise because the product will be applied into inkjet industry for precise usage such as labeling on batteries or pharmaceutical printing on pills.

Glitter deposition on unique designs require different amounts of glitter while printing. Some designs have a larger adhesive area and need to add more glitter. The dimple deposition roller mechanism satisfies the client requirement for easy control, which means the deposition can come to full stop easily by pausing rotation. Calculating how many teaspoons of glitter added to the hopper can lead to the result of how many rotations needed to deposit glitter, which helps track the material use and reduce glitter waste.

### 5.3 Integrating bushing into roller design

A crucial feature of our design is the roller that collects and deposits the glitter from the hopper into the chamber. The roller requires some form of extension so that it can be manually rotated from the exterior of the prototype and successfully deposit the glitter. Initially, the team used a thumb screw that fit snug within the interior of the roller cylinder. It also allowed for a team member to manually twist the spade shaped head of the screw as it provided a good grip and lever. The diameter of the thumb screw was also proficient where it aligned and continued from the rod as an extension, fitting snug in between the chamber and hopper. An issue arose, though, where it required the user who was rotating it much effort to twist, resulting in a high torque. This was because of the friction occurring between the thread of the screw and the prototype. A screw has a rough surface, so the rigidity created friction and did not allow for a smooth and consistent deposition process.

The coefficient of friction between two materials in relative contact can depend on the pressure the materials impose on each other, surface roughness of the relative harder contact surface, temperature, sliding velocity, and type of lubricant such as oil. The lubricant can also represent a form of contamination or unwanted build up between the two materials. When analyzing the thumb screw, it was found that the thread creates a rough, uneven surface that would almost cut into the prototype, creating a significant amount of friction. Another variable that complicates the calculation to find the most efficient material and surface for this application is the fact that the 3D printed prototype has many tolerance issues. This ranges from the lengths being off as well as the finish, which is the primary concern for the analysis. Each of the prototypes would leave the printer with strands of excess plastic attached, as well as bumpy and rigid surfaces. The PLA material is common to have a higher surface roughness value. This along with the threaded screw provided for the most friction.

To address this issue, the team evaluated other surfaces and materials that provided a significantly less amount of friction. The team also used a file to sand down the surface in contact with the rod to create a more consistent, smooth, and even surface. After testing, it was apparent that a metal rod with a smooth finished surface would be satisfactory for this application. A plastic material rod was considered because of the lower coefficient of friction between plastic and plastic, but the surface roughness proved to be a larger factor that did not allow for a smooth process. The metal, although having a higher coefficient of friction than plastic, proved as the best solution because the surface was smooth and created less friction than the plastic on plastic. With the knowledge of a correct diameter, a round aluminum rod with an outer diameter of 0.25 inches was purchased. This correct diameter allowed for the rod to easily fit within the interior of the roller. The rod was effective, but still provided friction when rotating.


Figure 15: Aluminum Rod | Figure 16: Thumbscrew

After reviewing alternatives, it is realized that the application of a bushing would be most beneficial to the design for future modifications. The team’s approach was trial and error, while this approach would include research in finding a metal with the least amount of friction as well as developing an intentional design with the bushing. Bushings, also known as sleeve bearings, are made to slide over rods to provide an extremely low-friction motion. A bearing was considered in this design but was not the correct size and could also get damaged by excess glitter entering the interior of the bearing. With multiple calculations of the tolerance of the 3D printed dimple roller, the team would know the minimum and maximum tolerance measurements needed to be considered. The next steps would include finding a bushing specific to that tolerance, ensuring it would fit within the interior of the roller. The bushing benefits this design significantly because on one end, it fits snug into the roller, and on the other, it is a specific size diameter that will exactly fit a rod for turning. With the fit, the roller can then rotate very smoothly because the bushing is a type of bearing and allows for a much better function.

After more research, a polyurethane bushing resulted as the ideal material for a bushing. They handle abrasion, impact, and most importantly can be molded. With the tolerance issue with the 3D printed dimple roller, one end of the polyurethane bushing would be molded to the interior of the roller while the other would exactly fit the rod. Purchasing a Prothane Total Kit would deliver a bushing kit with various sizes, front/rear sway bars, strut rods. These would allow for a seamless drive. With the bushing perfectly sized to the interior of the rod and can be altered to the tolerance issue of the 3D printing, then all that is concerned about is addressed because the strut rods are designed to seamlessly fit the bushing. This allows for a significant decrease in resistance, solving the issue of friction.


Figure 17 -Example of Prothane Total Kit

### 5.4 Optimizing wind speed calculations

Background
With this coating chamber design that the team has chosen to move forward with, it was essential to find air flow speed that would be able to push particles backwards, without pushing the particles more than 4 inches, which would be too far and out of the back of the coating chamber. The red craftsman pump shown in figure 18 would not be sufficient for this application because it only has one wind speed, blowing at approximately 5.1 m/s, constantly blowing the particles much too far.


Figure 18: Craftsman Air pump that was far too strong even with limiting modifications

After a meeting with Integrity and talking about finding a new air source, it was recommended that the team invest in an aquarium pump to try and test with. This test has proven to be very successful. The aquarium pump shown in figure xx did exactly what it was supposed to do, blowing the particles back approximately 3 inches, no further than the length of the inside of the chamber.


Figure 19: Aquarium pump used to find optimal air speed of 0.15 m/s

The next step was to find this airflow speed coming out of the aquarium pump. This was done using an air meter accurate down to hundredths decimal place when measured in meters per second. A measurement of 0.15 m/s was recorded coming out of the aquarium pump.

Assumptions
For the sake of simplification, it will be assumed that this result of 0.15 m/s is in an undisturbed environment where the aquarium pump is the only wind that is in contact with the blades of the air meter. Also, it will be assumed that the airflow coming out of the air pump at 0.15 m/s is constant and will always come out of the pump at this speed.

Equations and Calculations
The relation of cross-sectional area and air velocity to volumetric flow was needed to relate the aquarium pump flow to the speed of airflow required from the air compressor for the air blade.

Volumetric Flow: QV = A* V

This simple concept was used to perform hand calculations that provided an estimate as to what the air meter should be reading when the outlet of the air compressor is blowing at the air meter before it plugs into the air knife. The following figure 20 shows a diagram of the air knife setup, showing where the air knife speed (VAK) needs to be equivalent to the aquarium pump (VAP), and shows where the air speed needs to be calculated and tested (VAC) with the air meter to ensure that the air knife air speed is equivalent to the aquarium pump.


Figure 20: Diagram showing Aquarium pump tubing and Air Compressor tubing, and a simplified air knife adapter.

Organizing the calculation into three distinct parts allows for a clear understanding of the task at hand.

3) Aquarium Pump Tubing (AP)

QV-AP = AAP * VAP

2) Air Compressor Tubing (AC)

QV-AC = AAC * VAC

3) Air Knife Outlet (AK)

QV-AK = AAK * VAK

In the following calculations, the goal will be to find the optimal velocity of the air coming through the air compressor tubing (VAC). After acquiring this value, the air compressor tubing is to be fed into the air meter and the settings are to be slowly turned up until the air meter reads this value. The settings of the compressor are then noted and saved for use in powder removal.

To find VAC, the first step is to set

VAP = VAK = 0.15 m/s

This is done because the air at the air knife outlet needs to be moving at the same speed as the air coming out of the aquarium pump if the glitter is to be blown in the same fashion. Next, the dimensions of the air blade are as follows:

- Air blade x Dimension (LBY) = 0.002 m
- Air blade y Dimension (LBX) = 0.185 m

The optimal volumetric flow of air that should be flowing through the air blade can then be solved for.

QV-AK = AAK * VAP

AAK = LBY * LBX

QV-AK = (0.002 * 0.185) * 0.15

QV-AK = 0.0000555 m³
/s

Moving on to the next step, set:

QV-AC = QV-AK = 0.0000555 m³ /s

This is done because the volumetric flow going through the air compressor tubing will be equal to the volumetric flow coming out of the air knife outlet. Next, the dimensions of the air compressor tubing are as follows:

- Air Compressor Tubing Diameter (DAC) = 0.0095 m | (3/8 inch)

The optimal air velocity that should be flowing through the air compressor tubing can now be solved for.

QV-AC = AAC * VAC

QV-AK = AAC * VAC

Rearrange:

VAC = QV-AK / AAC

AAC = π *(DAC

2
/4)

Solve:

VAC = 0.0000555 / (π *(0.0095² /4))

VAC = 0.78 m/s

What do these results mean?
To get an air velocity of 0.15 m/s at the air knife outlet, the air flow velocity to run the air through the air compressor tubing needs to be 0.78 m/s. The air speed of 0.78 m/s is to be achieved using the air compressor with the 3/8-inch (0.0095 meter) tubing provided and pointing at the air meter. The settings that achieve a result of 0.78 m/s on the air meter are marked for future use.

Moving forward
To ensure the chosen wind speed is optimal, further testing would be done and data would be required using the air compressor in figure 21 to confirm the hypothesis that VAC = 0.78 m/s is the optimal wind speed for powder removal. Results may vary based on external factors such as imperfections in the blade adapter and sharp turns in the air compressor tubing.


Figures 21 & 22 – Air Compressor needed to operate the coating chamber at the correct air speeds.

### 6 Engineering Specifications

### 6.1 Overall Summary

Many of the specifications required to make this design work have each had a difficulty of their own, but SEED team 16 was able to overcome most of these issues by testing and making small incremental adjustments to the prototype until the more problematic specifications began to pass. This process is exactly what took place to make some specifications like ID20 and ID100 work at all. Some of the specifications like ID30 and ID60 would pass the verification tests on the first try because these could be deliberately designed with the correct solution to these specifications in mind. In the end, the team was able to achieve a relative pass/fail rate of 86%, only failing on one specification, ID80.

### 6.2 Failures

ID80 stated that “the quantity of escaped glitter is shall not exceed a 2 on the designated glitter escape visual scale.” It did not pass the specification because the glitter escape rate was not able to average below a 3 on the designated glitter escape visual scale. The glitter would continuously fly out of the back of the chamber because there was too much volume of air coming in, blowing the glitter too far. This specification was one of the most important to pass, hence the large reduction in the relative pass/fail rate.

### 6.3 Moving Forward

A way to potentially change the outcome of this failure would be to make the air knife blade a thinner, perhaps lowering it from a 2 mm wide blade to a 1 mm wide blade. The reason this would change the performance of the ID80 is because with a 2 mm blade, the flow field is too thick and will take more time to break up over the length of the chamber. A blade that is 1 mm thick will have the same flow speed, but a smaller flow field. Essentially, a 1 mm opening is letting in approximately half of the air volume that would come in with a 2 mm blade, allowing the flow to break up much more rapidly along the length of the chamber. This would ensure that the glitter escape rate would be at least a 2 or below by keeping the excess glitter inside the coating chamber, while still removing it from the substrate. Present integrity industrial inkjet integration with a product that met most of their specifications

### 6.4 Excel Table Showcasing Each Engineering Specification

Table 2: List of Engineering Specifications


### 7 Conclusion

### 7.1 Successes and Failures

The team was able to successfully complete some of the more important main qualities of the design, such as ensuring that the adhesive is completely coated with no deformation of the desired pattern. It was essential to be able to fully coat adhesive without deforming the design to create a successful product, this was the first task the team completed. Next, team focused on adhesive can be layered on top of previously dried layers of glitter to stack up multiple layers of powder, meeting the demands multilayer coating. These two tasks are among the most important fundamental functions of the design. The team managed to succeed in completing these two tasks after doing multiple rounds of research and experimentation. On the other hand, the team was not able to fully optimize the system for removing excess glitter to utilize it for subsequent coatings. Too much glitter was escaping the chamber which meant the team failed to complete one of the most important tasks presented by Integrity. This was the most difficult part of the project because the team was too focused on making sure the glitter would be correctly applied to the adhesive, rather than saving the particles and preventing a mess from happening. Rightly so, because the team could not design a system for collecting particles if there wasn’t any data on what would be happening with the particles during the adhesion process. Collection and reuse of particles would have been the next focus of the project if the team had more time.

### 7.2 Overall Satisfaction

This was a very difficult but interesting project. Overall, the client felt the group made good progress throughout the duration of the year, rating the group for maximum performance for each sprint. Learning and forward progression took place every time a meeting was held, comparing and talking about the various technologies being implemented into the design, and endless conversations about changes to make to improve development. The client presented the group with a challenging task for which they do not yet have a solution of their own just yet, so what was most important was to make sure that the client was able to take what the group was finding and learning and attempt to use it themselves to make a working product. Unfortunately, the group did not come up with the blueprints of a design that could be taken to the manufacturing line that would work for the client as desired but did manage to present a collection of ideas and functionalities that the client can choose to integrate for further development of their own design.

### 7.3 Recommendations for Future Development

To further progress the development of the prototype, it is essential to break progress down into 3 different categories. Electronic automation, air knife remodeling, and particle collection/reuse. First off, the team was in the process of developing an electronic glitter deposition module that would be fully automated. This would allow for a uniform coating of glitter to be constantly fed into the chamber as the conveyor belt pulls through the substrate below. The process would consist of a time varying microcontroller code that regulates when the adhesive is coming into the box to turn on and off the introduction of glitter into the system. Secondly, the current air knife provides a surplus of air volume being introduced into the system, causing the particles to fly out of the back of the chamber. This is the reason ID80 failed the verification test. To improve upon this, as previously mentioned, the width of the air knife blade needs to be made smaller, decreasing the thickness of the air coming in. This would allow the air being introduced into the system to disperse much more rapidly across a shorter distance, potentially passing ID80 by not blowing the particles outside of the chamber. Lastly, to achieve the best results for the client, a sort of powder/glitter collection module needs to be designed to work alongside the coating chamber. This could simply be a stream of air that blows the particles into interchangeable collection chamber that would easily allow an individual to reintroduce the particles back into the hopper. With these 3 recommendations for future development in mind, the wedge design may be able to enter the production line as a functional layer by layer adhesive particle printer.

### 8 Impact Statement

Situation 1: To keep the testing environment clean in the lab and common area, the team had come up with an idea to purchase a storage box for testing. This idea would allow the team to contain the excess glitter inside the storage box while running testing and prevent glitter escaping to make a mess. It worked very well to contain the glitter while running tests, which guaranteed the other teams in the lab would not be bothered by excess glitter. The decision showed the team is very thoughtful as engineers and worked professionally when sharing the lab workspace.

Situation 2: To realize environmental-friendly testing procedure, the team reused the glitter from testing by recollecting the excess glitter back to the bottle so that it could be used for next testing. Even if there is still a small amount of glitter going to waste, the team would make sure to vacuum them to keep the testing area clean for the other group in lab. Glitter is microplastic and it has negative environmental impact if it travels through waterways and ends up in the ecosystems. These decisions reflect that the goals of the team as engineering students are not only to design a product for the industry, but also to retain an environmental-friendly testing procedure and source sustainably.

### 9 Lessons Learned

Throughout the entire year for the design, the team learned many valuable lessons such as SCRUM management, how to communicate with the clients and teammates, products testing, rapid prototyping, etc. There are two main lessons were learned from this project, which were prototyping tolerance issues and communication with client and teammates. These lessons were based on personal experiences of the team members and covered both positive and negative experiences. The lessons learned helped the team have a summary of the valuable experience and what to improve in the future.

One of the lessons learned by the team was related to prototyping tolerance issues. The mechanism design of particle deposition is mostly prototyped by 3D printing, therefore the 3D printing technology plays a significant role in the design process, while 3D printed prototype has some common defects and problems such as warping, cracking and delamination. Most of the assemblies of the design are 3D printed by fablab, there are a few times that the subassemblies did not match with each other when the parts were obtained from printer. GD&T is one of the critical lesson the team learned during the design process, especially when designing with Solidworks. However, even if the Solidworks design dimensions are precise and the parts match with each other, the 3D printed parts sometimes were not as expected. For example, when dimple roller deposition was printed, the dimple roller was supposed to rotate smoothly between the hopper and chamber, while the 3D printed roller had very rough surface with the dimples, which caused large friction when rotating between the hopper and the chamber. The team had to use sandpaper to sand down the small bumps on the rough surface. Lessons learned that prototyping methods shall be chosen flexibly according to the functionality of the part. Certain subassembly of the design may not be the best fit using 3D printing, it could be replaced by metal material like stainless steel which has less friction after it is prototyped by machine shop.

Another lesson learned by the team was related to team communication between teammates and clients. Throughout the entire duration of the project, the team was in constant contact with each other, every team member has been very communicative about planning, scheduling, assigning tasks, which helps the project keep moving forward. When there were different voices on the design directions, the team discussed what was the best plan according to the timeline and client requirements. Before finalizing the design on chamber shape, the team had rapid prototyped three other chamber designs, while the timeline has already moved onto the testing stage, some team member had new design idea but considering the timeline and compare the pros and cons of the designs, the team communicated with each other and asked for advice from mentor Professor Marshall and settled down the design onto the wedge shape box design. It was a critical moment for the team to choose which direction to go with the design. On the other hand, communicating with clients played a big role in the design process as well. The team has been communicating with clients very actively throughout the year. Weekly or bi-weekly meetings with Integrity helped the team give honest and transparent updates about what’s new in the design, what are working well, what are not working well, etc. to the clients. The clients from Integrity are very responsive to give advice and update their requirements. The team has learned that it is very important to have frequent check-in and update with clients. Even by the final stage of design, stepper motor automation control on the dimple roller deposition was approved by the client, therefore the team put the assembly in the continuing development section, which help the team bettered the design and got prepared for design night. Good lesson learned that it is important to communicate with the team and the clients frequently and transparently.

### 10 Project Retrospective

The most impactful Kaizen for Team 16 was the ability to produce and refine many versions of a 3D printed model to directly increase the success in distributing the glitter within the chamber of the device. The initial prototype looks vastly different from the final prototype, as well as the ones along the way. Each prototype had a purpose to disperse glitter most efficiently within the chamber and coat the adhesive that would move through the module.

This Kaizen was chosen because the one requirement the team struggled most to achieve was how to maintain the air flow so that it could disperse the glitter within the chamber. The designs show much variety in geometry when compared to each other. With each prototype, lessons and concepts were learned about how to better adapt and refine the chamber of the design to enable the flow to pick the glitter up from the ground and circulate it while fully coating the adhesive.

The Kaizen shows how the team was fully involved in improving operations, continuously throughout the year. The challenge to refine the design particular to the engineering specification allowed for a pursuit to the ideal prototype.

The Kaizen of refining the design to best distribute glitter impacted our sprints in multiple ways. With each sprint review, the team is expected to show the client an ‘increment’. The goal of the entire year’s project is to demonstrate a design that works and functions per requirements. When the first few prototypes failed to do so, the team had to go back to the drawing board. First, it is to understand why the design is not operating as expected. Second is implementing new techniques, analyses, and adaptations to the design and test again for new results. Each sprint provided motivation and decision making. Specifically, in Sprint 5, the team made an executive decision to move on from the prototype they had been developing for four sprints and start over with multiple models. This was a large step for it may seem it is back to Day 1, but really the foundational skills and concepts learnt from the previous sprints and designs allowed for the team to work efficiently in creating and adapting the final design. After moving forward with the “Wedge” and concepts carried over from the first prototype, the process of creating, testing, and adapting was second nature and led to a successful final product.

One aspect of SCRUM that worked well for the team was the SCRUM huddles scheduled three times a week. Each team member was accountable to attend, recap work previously done, state goals for the present meeting, and what they would like to be done in the coming week or meeting time. This aspect was effective because the project was always fresh in each team member’s mind and provided a fast and steady pace for the project. With each SCRUM huddle, the SCRUM board also proved very beneficial. It kept these tasks and goals in check and on schedule, providing reference to any member that needed a reminder of what needed to be accomplished for that sprint, who was assigned to a task, and when deadlines were.

One aspect of SCRUM that did not work well overall was the demand for dedication from the students. It shows great structure, but it also created a stressful and high paced environment that is overwhelming for students who are seniors in college, taking other classes, working jobs, and dealing with other personal things. It is important to have balance as a student, but the format of this class (SCRUM) did not allow for any balance. There was constantly a demand for finishing deliverables, attending meetings with clients and mentors, testing and providing advancements in increments, etc. To modify this aspect and make it more useful is complicated, for the SCRUM method is successful but at the cost of the students’ wellbeing. A solution is possibly to have fewer deliverables or at least in less detail so the students can understand what is required without consuming most of their time.

### 11 Product Review

The product satisfaction levels for both the client and the development team are both very high. Based upon feedback gathered from each sprint and their final thoughts on the product, the client is very content with the results the module delivers. The product operates as required, the client is pleased with the hard work and dedication the team put into the development, and many designs were produced and implemented over the course of the year. With designs varying in foundational concepts, the clients are also able to utilize those as inspiration for more designs or further develop them. The team is also satisfied with the final product for many reasons. So much work was put into this product, making the achievement and success all more worthwhile. The obstacles presented throughout the year pushed the team to work harder and finish strong, creating a final product that reaches requirements and fully functions as hoped.

The product backlog entails the list below, sorted in order of importance from most to least:

- FDR Paper
- Final Tech Documentation
- Solidworks schematics

- Sketch ups of design
- Tubing diagram
- Testing results
- Bill of materials
- FDR Presentation
- Automate hopper deposition with stepper motor
- Need motor housing?
- Gears?
- Wiring diagram?
- Video (extra credit)

With the completion of Sprint 7, the team is now tackling the last assignments and deliverables due for the End of Semester section. The team is prioritizing the FDR Report as well as the Technical Documentation Package because they have the closest due date. The presentation is next on the list because it is due when the team is to present, which is a few days after the report and tech package are due. All of these documents will be complete and submitted by their specific due dates. The items in the backlog regarding the automated hopper deposition stepper motor will not be completed for a few reasons. This endeavor was taken upon the team in the last week of sprint 7. It was not realistic to have a finished product, but it was something that the team wanted to explore to see how the design could be advanced. The mindset was determined that it would not be complete, but the goal was to at least start exploring the mechanism and address how it could benefit the design as a whole. It was never a customer requirement; therefore it will not be prioritized to complete. As of the video, it is for extra credit and the team is looking to be able to complete all other deliverables before that is taken up.

### 12 Budget Review

When approaching this project, a budget of $2,500 was provided. After producing prior art research, a better understanding of what was needed to initiate the creating and testing of this product. The team took a trip to Lowe’s to gather any materials that may be needed for the process. The team stayed well below budget, only purchasing what was needed. When an obstacle arose and a product was required for testing, an order was put in and delivered to continue with testing and production. In review, the team finds that they were hesitant with the funds and could have purchased more at the beginning of the year so that there would be less time waiting for products to come in and be delivered. Having the assurance that it is acceptable to purchase materials that may not be needed instantly but good to have at a moment’s notice is a large takeaway and an aspect that might change to improve the success of future projects.

Below is a total detailed list of expenses, with a direct comparison of what was spent and the allotted budget.

Table 3: List of Expenses

Total Expenses | Cost
Craftsman inflator | $79.00
Glitter | $51.96
Mileage reimbursement | $106.06
Aquarium pump | $6.71
4 way pump valve | $7.99
Tubing | $7.55
Aluminum rod | $2.19
Stealth Ultra Quiet Air Compressor | $253.90
Primefit PCKIT26 Air Piping System | $84.97
Valve adaptor | $9.99
Handheld anemometer | $29.99
UVM Bookstore purchase | $34.27
Chemical Splash/Impact Goggle | $3.12
Kobalt 12-CT Comp Accessories Kit | $18.98
8 fl oz Elmer's Glue-All | $2.36
Duck tape | $2.83
66-QT Hefty Clear Storage Container | $15.18
FabLab 3D printing | $72.51
Total Spent | $789.56
Total Budget | $2,500.00
Total Leftover | $1,710.44

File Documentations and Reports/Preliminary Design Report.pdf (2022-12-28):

Preliminary Design Report – SEED Team 16 | 1

# Preliminary Design Report

## ______________________________________________

Project – Zen and the Art of Glitter Deposition

SEED TEAM 16:
Anthony Vieriu
Emma Marston
Helen Wang
Jake Varakian
Date | Revision | Release Notes
12/10/2021 | 01 | Initial Release

## Table of Contents

## Problem Statement

Our client is Integrity Industrial Inkjet Integration, a company that applies inkjet technology to design innovative production lines across various industries. The client would like the group to develop proof of concept for a module that will coat a layer of adhesive with glitter and reuse any glitter that does not stick. The module would be used in tandem with their current inkjet and UV curing light setup to stack layers of powder and adhesive. The module would improve production efficiency and save material across several industries. The current method utilizes a curtain of powder, which results in large amounts of waste material. By only using a small amount of powder and mixing it around a small container, the module would effectively utilize all the material for coating instead of creating a powder curtain.

The main functions required for this device are to control the amount of glitter deposited, ensure the adhesive is completely coated, and remove any excess glitter. Solving this problem will impact many manufacturing industries for it will be a new way to 3D print certain products, with a buildup of powder running through multiple times. It will also enable Integrity to build upon the concept and create a new line of manufacturing for them.

## Customers’ Requirements

The group identified three potential customers and produced a table of prioritized requirements based on the needs of each of the clients. The three customers were: Integrity, the customers of Integrity, and conveyor technicians. Each requirement was given a score to represent its importance to each customer and each customer was given a different number of points to represent the weight of their opinion.

Table 1: Customer Requirements

Customers | | Requirements
Integrity | Integrity’s Customers | Conveyor Technicians | Category | Requirement
5 | 3 | - | Functionality | Must be able to easily run multiple colors of glitter when running in series
13 | 10 | - | | Remove excess glitter without removing adhered particles
15 | 10 | - | | Glitter covers the adhesive efficiently
9 | 5 | 10 | | Ensure minimal glitter escapes the box
6 | - | 5 | | Box must be securely mountable to Integrity’s conveyor system
10 | - | - | | Must not take up too much space on Integrity’s conveyor
5 | 5 | 10 | | Operates for long durations reliably

13 | 7 | | | Glitter must be randomly and evenly distributed across adhesive
8 | 5 | 10 | Safety | Box must have zero risk for particle ignition
8 | 5 | 10 | | A way to easily control device to stop or divert the glitter flow
8 | - | 5 | Aesthetic | Box shall have a way to clearly observe particle flow within it

The three highest scored requirements for each client have been bolded in the above table. For Integrity and their clients, the top three requirements match as their priorities are similar. For the conveyor technician, the highest-level requirements focus on potential hazards when operating the module.

The highest-level requirement for both Integrity and their clients was, “Glitter covers the adhesive efficiently”, this is a fundamental function of the module. One of the main purposes of the module is to reduce material waste, if this cannot be accomplished then the module has failed. Both Integrity and their clients want to have the best coating while using the least amount of material. The second high-level requirement for Integrity and their clients was, “Remove excess glitter without removing adhered particles”. This is an important requirement because if glitter that has been adhered gets removed work has effectively been undone and that material cannot be used again. This requirement shares the same source of relevance as the first, Integrity and their clients need the box to perform its core functions and if adhered glitter is removed then the box has failed. The third high-level requirement is that “Glitter must be randomly and evenly distributed across adhesive”. An important function of the module is that a part should have a full coat of glitter after one pass through the module. If there are patches where no glitter lands, the process of stacking multiple layers would result in an uneven and rough three-dimensional surface.

The high-level priorities for the conveyor technicians focus on making the module easy and safe to operate. The first high-level requirement is “Box must have zero risk for particle ignition”. The module is intended to be used with a wide range of powders, including some powders that are flammable. Ensuring the safety of the technician and other individuals near the module is a necessity. Because of this, any risk of ignition must be mitigated. The next high-level requirement is, “Ensure minimal glitter escapes the box”. As a conveyor technician, making sure the line runs smoothly is very important. Powder being blown out of the box could be a hazard for any individuals in the vicinity of the box, additionally expelled powder could interfere with other components on the production line. The third high-level requirement is, “A way to easily control device to stop or divert the glitter flow”. In the case that something does go wrong, being able to rapidly halt the flow of glitter could reduce the risk to both operator and other components on the production line.

## Working Design Concept

The latest increment successfully accomplished a select few customer requirements. Firstly, being able to mount onto Integrity’s conveyor successfully, allowing the conveyor belt to pass through the 7.5-inch inlet and exit holes. Next, the team was able to successfully control the amount of powder fed into the chamber successfully by rotating a gumball like dispenser inside of the hopper that will drop roughly one teaspoon of particles into the chamber per every rotation. In the figure below, this is a perspective from underneath the coating chamber showing that the gumball deposition mechanism deposits approximately one teaspoon of glitter into the chamber.


Figure 1: Glitter Box 3D Print Prototype

The team is still working on some other requirements that are not yet functioning as intended. For example, in Figure 1, air vent holes can be seen on the side of the chamber, these holes are there to balance the pressure inside the box by letting air escape while air is being pumped into the chamber. The smaller particles tend to fly out of these holes and an alternative method of relieving pressure will need to be developed. Another work in progress is the air inlet on the side of the conveyor exit, it is not shaped very well and needs to be redesigned to allow multiple different types of nozzles/inlets to attach to the system.


Figure 2: Vision from the Bottom of the Design

When adapting the Solidworks model to the current 3D printed increment shown above, multiple steps were taken to ensure client satisfaction. The chamber was lengthened so the inlet and outlet at the bottom of the design was measured to be both 7.5 inches long so the conveyer could smoothly operate under the device. The width of the chamber itself was made skinnier to take up less space on integrities conveyor. These two adjustments decreased the volume of the coating chamber. Next the air knife inlet was reformed relative to the sizing of the new skinnier design. The redistribution channel was also changed, initially, it once fed into the bottom of the chamber but was repositioned to fit into the top near the hopper in order to promote better mixing of the air flow and the particles. The hopper was decreased in size because there was no need to hold as many particles as the team had initially tried to account for. Lastly, the vent holes were made larger because there was a need to accommodate for the large influx of air entering the system. The reasoning behind the modifications made can be referenced to Key Analysis 3 where the alterations were made based off principles demonstrated in Bernoulli’s Equation. The latest version of the increment can be seen below in figure 3.


Figure 3: Solidworks Design displaying different components of the coating chamber

## Analyses

### Key Analyses 1: ANSYS/Fluent Simulation

As the first prototype was printing the team had already planned on making changes and producing a second. Since the first prototype hadn’t finished printing yet and physical testing was limited in terms of what measurements could be made, Computational Fluid Dynamics was considered. The CFD would be used to obtain more detailed information about the flow within prototype 1 and that information would be used alongside physical testing results to make design decisions for prototype 2. ANSYS/Fluent was used to run the CFD, these programs use the continuity equation and the Navier-Stokes equation to solve for basic flow characteristics.

Continuity: ∂ρ
∂t + ∇ ∙ (ρv) = 0

( 1)

Navier-Stokes: ρ(

dV
dt

+ v ∙ ∇v) = −∇p + μ∇

2v + f

( 2)

The SolidWorks model of prototype 1 was exported into ANSYS Workbench where a volume extraction was used to mesh the space where air would be flowing through the box.


Figure 4: Interior Fluid Mesh | Figure 5: Exterior Solid Mesh on top of Fluid

A sphere of influence meshing method with the center located in the middle of the coating chamber was used to obtain a fine mesh of 344327 finite volumes for the interior fluid. There would be no flow through the solid, so the default coarse mesh was left untouched. This mesh was then exported to Fluent where the simulation parameters were set.

A pressure-based transient simulation was used, with gravity considered at the standard -9.8 m/s^2. The discrete phase model was enabled for the potential to inject solid particles into the flow in future simulations. Air at standard conditions of ρ = 1.225 kg
m³

and μ =
1.225 kg
m∗s

was specified as the fluid to be used. The air blade inlet was specified as a velocity inlet with a velocity magnitude of 100 m
s

normal to the boundary. Both the velocity magnitude and direction of the
inlet may be altered in future simulations to


explore how different inlet velocities and angles
change the flow within the box. All other boundaries were designated as pressure outlets into atmospheric conditions and the solid box was designated as a wall. The simulation was then initialized and ran for a total flow time of 5 seconds with a time step of 0.1 seconds. 100 iterations were run per time step to ensure simulation convergence.

After the 5 seconds of flow time were finished running, the data was exported to Tec Plot for formatting and analysis. The main results of the simulation were animations of velocity contours in the X, Y, and Z directions. These animations allowed the group to get a more detailed view of the flow within the box and to better understand what changes needed to be made for the next prototype. The X-velocity and Y-velocity animations showed the group that air was flowing as anticipated. The flow entered through the inlet and swept across the conveyor outlet, then it followed the redistribution channel before swirling around the coating chamber. This confirmed that the group's initial guess on how the air would flow was correct.


Figure 7:X-Velocity contour at t=4.1 seconds | Figure 8: Y-velocity contour at t=2.9 seconds

Figure 6: Labeled boundary conditions

One issue was noticed within the X-velocity animation once streamlines were implemented. As the flow progressed, areas of interference were noticed within the flow. Particularly at the base of the redistribution channel and at the right end of the coating chamber. Patches of air flowing opposite to the intended direction created spirals that disturbed the flow. Interference in the flow within the chamber
could lead to potential issues with coating in
the future.


In addition to the flow interference noticed in the X-velocity contour, another potential issue was noticed in the Z-velocity contour. Throughout the entire 5 second simulation there was a significant amount of airflow directed towards the conveyor outlet. This flow could carry glitter out of the box instead of directing it back into the coating chamber. As containing the glitter within the box is a high-level customer requirement, fixing this became a priority.

Both the issue shown by the
streamlines and the issue shown by the Z-velocity contour could be detrimental to the project, addressing these issues became a high priority for prototype 2. The group came up
with two broad solutions to both issues, the
first being, changing the way air is being
added to the box. This could be in the form of adding an air curtain to the conveyor outlet to prevent outflow, or perhaps changing the air inlet to blow with less force across a wider area. This solution caters nicely to CFD resources, as adding an air curtain or changing properties of the inlet is very easy to do computationally. The second conceptual solution is to change the geometry of the box to prevent these issues from occurring. This solution would take
additional time as a new SolidWorks model
would need to be conceptualized and


subsequently modeled. However, the group is already planning on producing a second SolidWorks model which will be put through a similar CFD simulation to compare to the first prototype. Moving forward, SolidWorks modeling and additional CFD will be used in tandem to determine the most desirable characteristics for the second prototype. As the team moves into the second semester of the SEED program additional simulations will be run to gain additional

Figure 9: X-velocity streamlines at t=2.5 seconds

Figure 10: Z-velocity contour at t=2.7 seconds information on the flow, this includes injecting particles into the flow via the hopper boundary layer to see how the box will act in a situation that more closely parallels reality.

### Key Analysis 2: Nozzle Analysis

To achieve the requirements that glitter covers the adhesive efficiently, it is important to make sure to have a steady laminar air flow to make the glitter circulate inside of the prototype. Due to the latest testing showed the issue that the air pump wasn’t able to provide the air flow strong enough to make the glitter circulated inside the glitter box, the team purchased Craftsman air pump which provides faster velocity and higher pressure of the air flow. The equipment came with multiple nozzles and each of them has different shapes. It is important to analyze the nozzle shapes and functionalities to choose the best fit for the prototype testing. From the previous testing, the team has tried the cleaner with thin long tube as nozzle, and mattress air pump with short cylindrical shaped nozzle, each of the nozzles performed differently while running the testing. It shows significant difference in air mass flow rate and pressure gradient inside the glitter box design.

To compute the mass flow rate of air, here is the theoretical equation for nozzle.
Nozzle Mass Flow Rate¹-
---> v=Ṁ/ρA ρ= density (STP: 1.225kg/m³⁾ A= cross sectional area (m²

)
| v= velocity (m/s) By knowing the mass flow rate of different types of nozzles, it enables to choose the best

one for the nozzle needed. As the equation above, the smaller cross-sectional area, the higher air velocity.


1

Figure 11: Nozzle Analysis: Compressible Mass Flow Rate

1 Sourced from NASA website: https://www.grc.nasa.gov/www/k-12/rocket/nozzle.html

To analyze the air velocity and pressure provided by the nozzle, fluid mechanics theory knowledge is used here to explain the velocity and pressure gradient of the air flow in the nozzle. As the figure shown below, assuming a fully developed flow is provided by the purchased air pump and added to the glitter box, according to fluid mechanics theory, here are four types of nozzle model as options to analyze. In the first stage, it is the type of nozzle that has straight cylindrical shape. The velocity gradient of the air flow is zero, which means the air flow speed is constant. The pressure gradient is a negative constant, which means it is linearly decreasing. For the nozzle type two, it is a stage with the decreasing cross-sectional area. The pressure is decreasing while velocity is increasing. In stage 3, it reaches the minimum cross-sectional area, pressure value gets to the minimum while velocity value gets to the maximum. In stage 4, cross-sectional area increases, pressure value increases while velocity value decreases.

In conclusion, the theory above shows that the long hollow cone shaped nozzle provides the highest velocity and that is the type of nozzle which applies the best for the increment.


Figure 12: Nozzle Analysis: Velocity & Pressure Analysis

Figures shown below are the nozzles applied to the design during testing. The figure # on the left was about the nozzles applied at the beginning of the testing procedure. The nozzles match with the first pump used for the testing, since pump power wasn’t able to provide strong enough air flow, the team changed device, however, the nozzle on the right of the figure # happened to provide the fastest air flow rate, which proved the fluid theory above. The nozzle in figure # is the one matches with the Craftsman air pump, which enables the glitter to circulate inside the glitter box successfully. The nozzle analysis helps give a perspective for improving a better laminar air flow inside the glitter box design. On the other hand, it provides the team with another direction to develop the increment in the next step.


Figure 13: Nozzles for Testing (pump 1) | Figure 14: Nozzles for Testing 2 (Pump 2 Craftsman)

### Key Analysis 3: Product Development

The structure of the prototype evolved after speaking with both clients and Dr. Marshall. They offered input that would benefit the functionality of the device. After the first Solidworks design as seen in Figure 15, the team was able to see what needed to be altered.


Figure 15: Orthographic View of Design 1 | Figure 16: Top View of Design 1

In Design 1, the team included key features. With the exact measurement of the conveyer belt provided by our client, the group formatted its length and the orientation of the design so it would apply the glitter correctly to any material passing underneath. Next, the ‘gumball’ dropper was designed with an airtight seal, so no glitter could escape from the top when it is rotating through, scooping the glitter, and then dropping it. The deposition chamber is designed to hold a large volume, so the refill process requires less maintenance. With the addition of an air knife, the powder can be fed back into the system. This allows for little to no glitter to escape. Lastly, because the team implemented compressed air into the system, there needs to be points of pressure release. If this is not accomplished, the air will not circulate, and it will try to escape with enough force. This would lead to many issues because the air, as well as the glitter, would escape through the top where the glitter is originally deposited, or towards the seal along the conveyer belt that is supposed to be kept clear of extra particles due to the air knives. These issues are addressed with the creation of the air vents on the side, as you can see in Figure 18. These holes on each side of the design relieve the pressure, without the glitter escaping through.


Figure 17: Demonstration of Bernoulli’s Equation

Using the kinematic form of Bernoulli’s Equation and the concepts supporting it, a more detailed analysis of the module was conducted. Dr. Marshall is well acquainted with fluid mechanics and gathered insights for the team to delve into. Figure 17 shows a basic demonstration of the principle. As velocity of a fluid in motion increases, in this case air, the pressure within the moving fluid decreases.


Figure 18: Orthographic View of Design 2

With a better understanding, new revisions were made to the Solidworks design. At the top of the design, the changes included reducing the hopper size and reducing the chamber size. The group found it unnecessary to have such a large hopper. Minimizing the size allowed for less chance of error with glitter escaping. The goal of lengthening and decreasing the size of the chamber was to alter the direction of the air flow once it entered the chamber and started to circulate. This would potentially help with redirecting the recirculating flow so it may create turbulence. Changing the geometry of the design has drastic effects on the streamline of the air flow, something the group is still discovering and experimenting with. Other alterations involved reducing the air knife inlet so there is less of a gap for glitter to escape from. Creating a tunnel at the inlet allows for a more directed flow instead of just a slit seen in Design 1. The group found that there was a need for more pressure relief, so the vent size was increased on each side to stabilize the pressure equilibrium. It is necessary to apply positive or neutral pressure within the system because the conveyer belt system does not operate well with any vacuum or negative pressure. Lastly, mounting holes were added so the product could be attached to the conveyer belt system at Integrity.

After testing in Sprint 3, the team found it was necessary to consider other ways to manipulate the air flow within the chamber so the glitter particles can be swept up and circulated. After analyzing the pattern of the flow and using the principles of Bernoulli’s Equation in Figure 17, developing a better understanding of pressure, some alterations have been theorized that will increase the performance of the device. First, the size of the inlet would be increased. It currently has a small entry where high velocity enters the device and is driven into a low-pressure unit. It is desirable to create a laminar flow before or as it enters the device so that the pattern of the streamlines is more direct. The 180° turn consists of a narrow channel. It is already difficult to change the direction of air flow, and for it to be directed towards a high-pressure area is even more difficult because the fluid is attracted to low pressure. In this current setup, turbulence is the result. Widening or enlarging that channel in general will decrease turbulence. Lastly, the team is proud of the results coming from the hopper and gumball deposition design, but there are plans to advance it. The new adaptation would involve a more gradual deposit of the glitter, instead of scooping once and dumping all the glitter. This is being done for multiple reasons. First, it would make the glitter deposition more consistent and be less glitter dumping at once, but more frequently. Next, it is much more feasible to carry a particle in the air when it is more scattered compared to being a part of a large clump.

### Key Analysis 4: Particle Sizing and Settling Rate

The process of finding out how to make the design work has proven to be challenging, however there are certain ways that it works better than others. For example, what works the best so far is using larger particle sizes that do not weigh very much at all, meanwhile what works the worst is using small particles that weigh more. It was not very easy to get to these small particles to blow around. At first this concept made sense because but there was no research done showing how particle size might affect our design, the team wasn’t able to fully grasp why these smaller particles weren’t mimicking the larger ones. This prompted an expansion of research to begin. After speaking with Professor Marshall about the project he suggested investigating the settling rate of the particles. At this point, quite a bit of testing had been done and the team learned a lot about the project, but it wasn't until the research began on how the settling rate may affect the flow of the particles that the team realized how vital this sort of analysis is for the project. The door has now been opened to understanding the results that the testing is producing. In the figure below, figure 19 the equation for the settling velocity of particles is shown along with its parameters and what each one means listed in the figure.


Figure 19: Settling Velocity

The settling velocity of the particles shows how quickly a particle will fall to the ground. Essentially it is an equation that determines the terminal velocity of a particle and is useful because there is a direct correlation between the settling rate and how easily the particles can be blown around in an air flow. The only factors that will actively change from equation 10.1 are the mass density and diameter of the solids during the interchange of the different particle sizes. The rest of the parameters will stay constant because this device will always run at the same atmospheric pressure, and gravity will never change.

After understanding the concept of the particle settling rate the team was able to run another series of tests using four different particle sizes to further understand the theory of the settling velocities. Large paper particles, medium size plastic particles, and glitter particles that came in small and tiny sizes were used during these tests, they can each be seen in the following image, figure 20.


Figure 20: Displaying different particle sizes

When using a compressed air can as the source for each particle size, each particle reacted differently relative to one another. The large particles successfully traveled through the coating chamber, flowing through the correct path with very few flowing the wrong way. Firstly, this is because the air in the system tends to flow similarly to the way that the team intended, secondly, because the density of paper is very low, and the diameter of the paper particles is larger, so the flow can easily lift and blow the paper particles along the path the flow is already moving. The medium plastic particles had a smaller diameter than the large ones, and a higher density, so not many of them were able to flow along the correct path as easily. The small and tiny glitter particles both had approximately the same density as the plastic but had a much smaller diameter, so these particles were the most difficult to blow around and very few managed to flow along the correct path. This explains why the large paper particles were the only ones to successfully flow through the chamber, and why the three smaller particle sizes, glitter, and plastic, failed, and only had very few particles that were able to successfully flow through the chamber. The results are very interesting because it shows that the compressed air can was unable to produce a flow strong enough to blow some particles, however, was strong enough to move some.

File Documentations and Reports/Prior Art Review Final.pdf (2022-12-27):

# Prior Art Review

_____________________________________________________________________________________

Project 16 – Zen and The Art of Glitter Deposition

Team Members:
Emma Marston
Anthony Vieriu
Jake Varakian
Helen Wang
Date | Revision | Release Notes
10/10/2021 | 01 | Initial Release
12/10/2021 | 02 | Second revision, corrections made

Project 16 | Prior Art Review – Revision 01 | 1

## Table of Contents

4.1 Journal Article: Preparation and performance characteristics of an environmentally-friendly

4.2 Journal Article: Reducing Respirable Dust Levels During Bag Conveying and Stacking Using

### 1 Search Process

### 1.1 Overview

To begin the search process, it was decided that each team member would be responsible to produce a minimum of 3-5 different search terms in the search log as well as presenting the most relevant source they found to the rest of the team. Searches were to be recorded as they found them to prevent any repeating work . Each type of prior art should be reviewed (Journals/articles, Standards, Patents) to get a comprehensive understanding of the available prior art. The client indicated that there was not much prior art directly pertaining to the project, so the team focused mostly on finding ideas that could be partially implemented or create inspiration. The searching process mostly followed the pattern of finding a journal or article with some degree of relevance to the project, followed by further exploration of the relevant terms via additional journal searches as well as patent searches. This method often resulted in one search log entry leading to several more relevant terms. In the case that a search did not yield any relevant information, the terms and location of the search were still recorded to assist other group members.

### 1.2 Challenges

The group ran into several problems towards the beginning of the prior art process, but many of these issues were resolved by becoming more comfortable with the search process. As the client had mentioned, the prior art specifically related to the problem was limited. It took some time to find relevant information regarding the project for each search because most sources did not relate or benefit. Additionally, once a potential source was found, usually only an exceedingly small portion of the information was relevant. Many searches would begin with something that sounded relevant and ended up leading to a dead end. This was a big problem because of how challenging it was to find any information relevant to the project. The group then had a meeting to compile a list of search terms to try and help initiate the searches. These search terms were able to produce some new and relevant information which helped to progress the search.

Additionally, the group ran into some issues with the search for standards. At first it was difficult to determine what kind of terminology should be used for the search as “glitter boxes” are not a typical product. After some dead end searches the group came upon ASTM standards for additive manufacturing. While inkjet processes and powder deposition were not exactly mentioned, they do qualify as additive manufacturing and this standard was deemed relevant. The standards presented were helpful but should be further investigated. The standards specifically state 3D printing, the problem put forth by the client could certainly be considered additive manufacturing.

### 1.3 Effectiveness/Satisfaction

With each search, the team members were able to learn how to change key words to come across better articles, journals, or patents that related more to the project at hand. Learning what not to search was as beneficial because it narrowed down the results and gave the team a better sense of what to find that could help develop the project. The team was satisfied with our work and process of searching. We were somewhat satisfied with the results found after searching, but would have found it beneficial to find some patents or articles pertaining more to inkjet systems so the team could have a better understanding of the operation and functionality.

Once the predetermined number of searches and sources were found by each team member, a meeting was held to communicate the most relevant information found by each member and determine if the search log should be concluded. The information shared in this meeting led to several ideas which would contribute to the development of the first sprint’s increment along with the project as a whole. The most relevant sources were agreed upon and a more comprehensive understanding of each source was obtained and documented below. It was at this point that the group decided to conclude the search log due to the significant amount of information that had been found as well as the increasing difficulty in producing search terms. Even with findings that led to dead ends or did not relate to the project, these sources helped each team member become more aware of different techniques, machines, and uses for the same products we were searching. Knowing the different capabilities or systems similar help open doors to different concepts and uses that we did not know of before.

### 2 Search Log

Date | What are
you
looking
for?

Where did
you look?

Search Query Evaluation of the search.

9/23

Existing
solutions
for the
collection
of
particles
off a
surface

Professor
Marshall
N/A | -Professor Marshall forwarded several of his own articles relating to the use of bounded vortex flow to collect particles from a surface. These articles gave a potential solution for the collection portion of our problem. -Along with this he sent us a document explaining the Twister Cleaning Nozzle which was designed to “create a bounded-vortex flow field to aerodynamically remove dust particles from the surface of optic filters.” -While these resources are very helpful in beginning our prior art review, the client did not seem very receptive of the bounded vortex flow idea. Seemed to prefer simplified designs utilizing a single air blade
9/27 | Technique s used to evenly/ran domly distribute particles | Compendex | Particle deposition | -This search yielded an example of a system designed to test particle deposition based on surface roughness -The system used compressed air to blow particles into a chamber with the test surface and a fan -This system did not have any way to remove the particles -a second article demonstrated the effect of particle diameter and the use of a ribbed channel on deposition efficiency -while particle diameter could affect results in our final design, the client would not be able to disclose all possible powders that would be used
9/27 | Existing patents for material deposition | Google Patents | Material Deposition | -This search showed a method of additive manufacturing, to fabricate solids -while the client is performing additive manufacturing this type of patent is for precise addition/stacking of solids which does not apply to the adhesive powder system the client needs

9/28 | Potential
avenues
for
collecting/f
iltering
glitter

Google
Scholar

Dust Removal -This search yields an article exploring the use of an environmentally friendly agglomerant to improve dry dust removal in a filter material (“Preparation and performance characteristics of an environmentally-friendly agglomerant to improve the dry dust removal effect for filter material” –Liu)
https://doi.org/10.1016/j.jhazmat.2020.122734
-The article described the use of a pulse filter device which would periodically inject powder into a chamber with the filter material
-One of the included parts was a pulse valve which was controlled by a pulse controller, this same setup could be used to add turbulence to our glitter box. More research into pulse valve should be done
-Other aspects of the device recorded wind speed as well as dust concentration, these would not be relevant in our design unless the client wants an exact measure of how much glitter is left in the box
9/28 | Existing implement ation of pulse valves | Google Patents | Pulse Valve | -This search provided more insight into the various applications of a pulse valve as well as how they operate -One interesting patent was for a Variable orifice pulse valve; this could be useful when it comes to calibrating the turbulence in the glitter box. Too much turbulence could interfere with the adhesive and potentially disrupt the deposition process https://patents.google.com/patent/US6032667A/en?q=pulse+valve&oq=pulse+valve (https://patents.google.com/patent/US6032667A/en?q=pulse+valve&oq=pulse+valve)
9/28 | Standards for this kind of product | ASTM | Additive manufacturing | -This search led to several patents regarding the general principles, guidelines, and recommendations for any additive manufacturing -While the standards specifically state 3D printing, the problem put forth by the client could certainly be considered additive manufacturing. These standards should be further investigated
10/01-10/03 | Technique s to Apply powder | Google Patents | Powder Application | -This search led to many patents that are very similar to some of the sketches we made. Showing many different ways powder can be applied to a surface. -Many new search terms search terms came from this search and each one needs to be searched. -More research into powder applications needs to be done, lots of good information here. -https://patents.google.com/patent/US10548695B2/en?q=Powder+Application (https://patents.google.com/patent/US10548695B2/en?q=Powder+Application) here in this patent, we can find information similar to what we are
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

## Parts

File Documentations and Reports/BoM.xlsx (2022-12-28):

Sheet: Cover
Project 16 - Glitter Deposition
Bill of Materials
Revision History
 | Revision | Date | Description of Change
 | A | 2022-03-23 | Preliminary Draft
 | B | 2022-05-05 | Final Release

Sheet: BoM
Bill of Materials |  |  |  |  |  |  |  |  |  | Supporting documentation
Item Number | Part Number | Description | Part / Assembly | MFG | MFG Part Number | Units | $/Unit | Qnty | Cost | Vendor | Notes
10 |  | Wedge Assembly | Assembly
10.1 | 1001 | Wedge Frame | part | UVM Fablab | 3076 | each | $23.16 | 1 | $23.16
10.2 | 1002 | Blade Adaptor | part | UVM Fablab | 3076 | each | $11.04 | 1 | $11.04
10.3 | 1003 | Plexi Glass | part | UVM Fablab | 3125 | each | $0.00 | 1 | $0.00
20 | 1004 | Stealth Ultra Quiet Air Compressor | part | Amazon | B07N1ZC8PZ | each | $199.00 | 1 | $253.90
30 | 1005 | 16 oz glitter bottle | part | Craft & Party | 4340000000 | each | $12.99 | 1 | $12.99
40 |  | Deposition Assembly | Assembly
40.1 | 1006 | Aluminum rod | part | K & S Store | 83045 | each | $2.19 | 1 | $2.19
40.2 | 1007 | Offset hopper | part | UVM Fablab | 3537 | each | $2.49 | 1 | $2.49
40.3 | 1008 | Dimple Deposition | part | UVM Fablab | 3128 | each | $2.19 | 1 | $2.19
50 |  | Pump Assembly
50.1 | 1009 | Primefit PCKIT26 Air Piping System | part | Amazon | ‎PCKIT26 | each | $84.97 | 1 | $84.97
50.2 | 1010 | Valve adaptor | part | Amazon | CT3438 | each | $9.99 | 1 | $9.99
60 | 1012 | String | part | UVM Bookstore |  | each | $3.99 | 1 | $3.99
70 | 1013 | Duck tape | part | Lowe's | 377064 | each | $2.83 | 1 | $2.83
 |  | Here are tickets throughout the year:
 |  | 3D Printing: Ticket 2847 | Gumball+Body |  |  |  | $7.40
 |  | 3D Printing: Ticket 3056 | Rollover design (2) |  |  |  | $13.33
 |  | 3D Printing: Ticket 3128 | Nozzle for anthony's |  |  |  | $0.19
 |  | 3D Printing: Ticket 3128 | Acrylic for anthony's |  |  |  | no cost
 |  | 3D printing: ticket 3120 | Frame for anthony's |  |  |  | $12.71
 |  | 3D Printing: Ticket 3128 | Dimple Deposition |  |  |  | $2.19
 |  | 3D Printing: Ticket 3537 | Hopper |  |  |  | $2.49
 |  | 3D Printing: Ticket 3076 | Wedge design+ acrylic |  |  |  | $23.16
 |  | 3D Printing: Ticket 3366 | air blade adpaters(3 nozzles) |  |  |  | $11.04
 |  |  |  |  |  | TOTAL | $72.51
 |  | Total Expenses | Cost
 |  | Craftsman inflator | $79.00
 |  | Glitter | $51.96
 |  | Mileage reimbursement | $106.06
 |  | Aquarium pump | $6.71
 |  | 4 way pump valve | $7.99 |  |  |  |  |  |  |  |  | 10
 |  | Tubing | $7.55
 |  | Aluminum rod | $2.19
 |  | Stealth Ultra Quiet Air Compressor | $253.90
 |  | tubing and nozzles | $84.97
 |  | Valve adaptor | $9.99
 |  | Handheld anemometer | $29.99
 |  | UVM Bookstore purchase | $34.27
 |  | Chemical Splash/Impact Goggle | $3.12
 |  | Kobalt 12-CT Comp Accessories Kit | $18.98
 |  | 8 fl oz Elmer's Glue-All | $2.36
 |  | Duck tape | $2.83
 |  | 66-QT Hefty Clear Storage Container | $15.18
 |  | FabLab 3D printing | $72.51
 |  | Total Spent | $789.56
 |  | Total Budget | $2500.00
 |  | Total Leftover | $1710.44

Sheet: Instructions
Item # | Sequential Number for referencing. You can use "." to create sub assemblies to match your assembly structure.
Part Number | Unique part numbering system created by your project. This allows for you to use alternate mfg parts without changing you drawings. Example: 1000, 1001, 1002… All drawings you create should have PN's if they are manufactured, assembled, etc.
Description | Description of part
Part/Assembly | Identify if this is a part or an assembly in your BoM.
MFG | Part manufacturer
MFG Part Number | Manufacturer part number
Units | Units - each, m, box of 100, etc
$/Unit | Cost / unit of the part
Qnty | Quantity used in the assembly
Cost | Cost for the assembly

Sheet: BoM - Example
Bill of Materials |  |  |  |  |  |  |  |  |  | Supporting documentation
Item Number | Part Number | Description | Part / Assembly | MFG | MFG Part Number | Units | $/Unit | Qnty | Cost | Vendor | Notes
10 | 1000 | Motor Assembly | Assembly |  |  |  |  | 4 | $492.00
10.1 | 1005 | 24V motor | part | Acme Corp | 12345 | each | $100.00 | 1 | $100.00
10.2 | 1010 | 5V quadrature encoder | part | US Digital | 4456 | each | $20.00 | 1 | $20.00
10.3 | 1034 | M4 Set screw | part | Fastenal | 2345 | each | $1.00 | 3 | $3.00
20 | 1001 | Skateboard chassis | part | Custom | n/a | each | $300.00 | 1 | $300.00
30 | 1002 | Grip tape | part | TapeR | G-345-H | 10' | $20.00 | 1 | $2.00
40 | 1012 | Battery Holder Assembly | Assembly
40.1 | 1004 | Battery | part | Powersonic | 56R4512 | each | $40.00 | 2 | $80.00
40.2 | 1006 | Battery Holder | part | Custom |  | each | $30.00 | 1 | $30.00
40.3 | 1036 | M6 x 30mm | part | Fastenal | 3425 | each | $0.50 | 10 | $5.00
40.4 | 1011 | 12AWG Wire, Red | part | Polar Wire | R12-100 | 100' | $75.00 | 2 | $1.50
40.5 | 1012 | 12AWG wire, Black | part | Polar Wire | B12-100 | 100' | $75.00 | 2 | $1.50
40.6 | 1013 | 20A, 120Vac male connector | part | Molex | M45-34 | each | $10 | 1 | $0.10
50 | 1014 | Gorilla Glue | part | Xcom | 4523 | bottle | $10.00 | 0.1 | $1.00

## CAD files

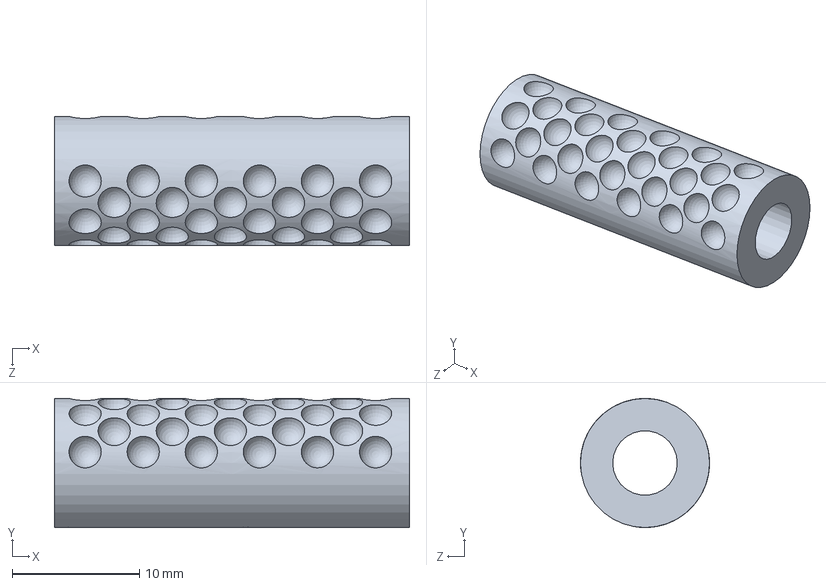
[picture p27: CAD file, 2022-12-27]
final version senior design/Dimple Deposition Part V3.SLDPRT
27.9 x 10.2 x 10.2 mm

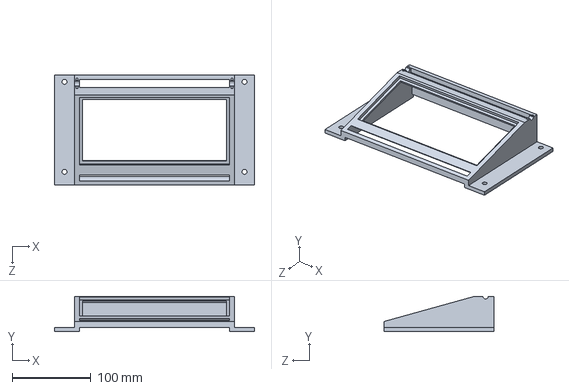
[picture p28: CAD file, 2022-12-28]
SolidWorks Models/Wedge Box 3.0.SLDPRT
254.0 x 44.5 x 139.7 mm

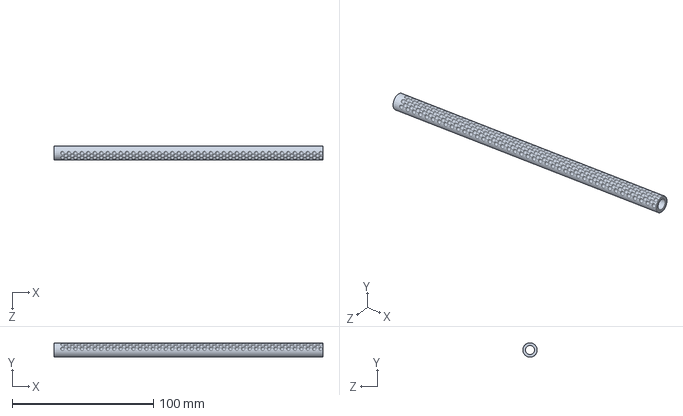
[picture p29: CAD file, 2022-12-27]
final version senior design/Long Dimple Deposition Part V3.SLDPRT
190.5 x 10.2 x 10.2 mm

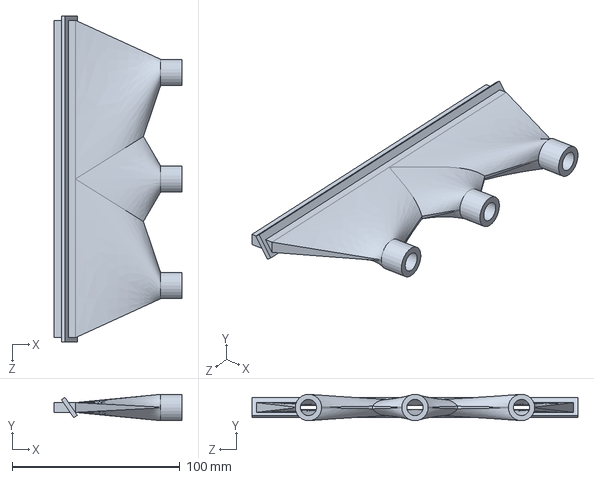
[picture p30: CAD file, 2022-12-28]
SolidWorks Models/Blade Adapter V3.1.SLDPRT
76.2 x 15.7 x 194.3 mm

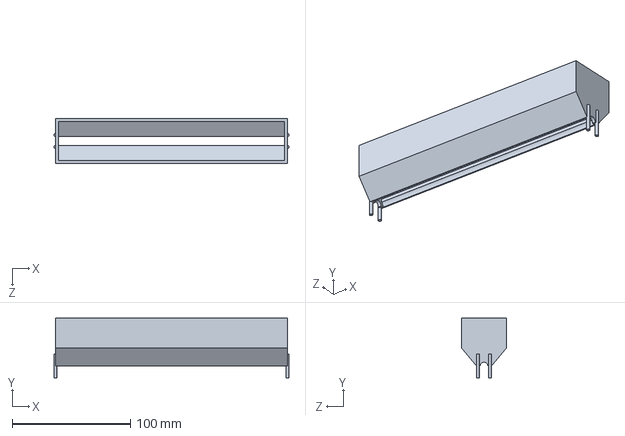
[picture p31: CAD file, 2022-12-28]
SolidWorks Models/Offset Hopper Long.SLDPRT
198.9 x 50.8 x 38.1 mm

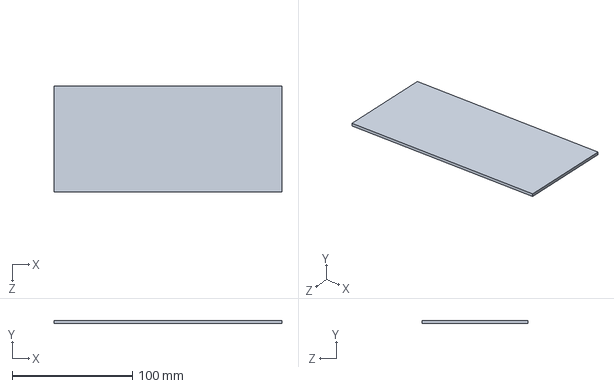
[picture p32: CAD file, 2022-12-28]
SolidWorks Models/Acrylic.SLDPRT
189.2 x 2.54 x 87.6 mm

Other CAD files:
SolidWorks Models/Long Dimple Deposition Part V3.SLDPRT
final version senior design/drawing for long dimple.SLDDRW

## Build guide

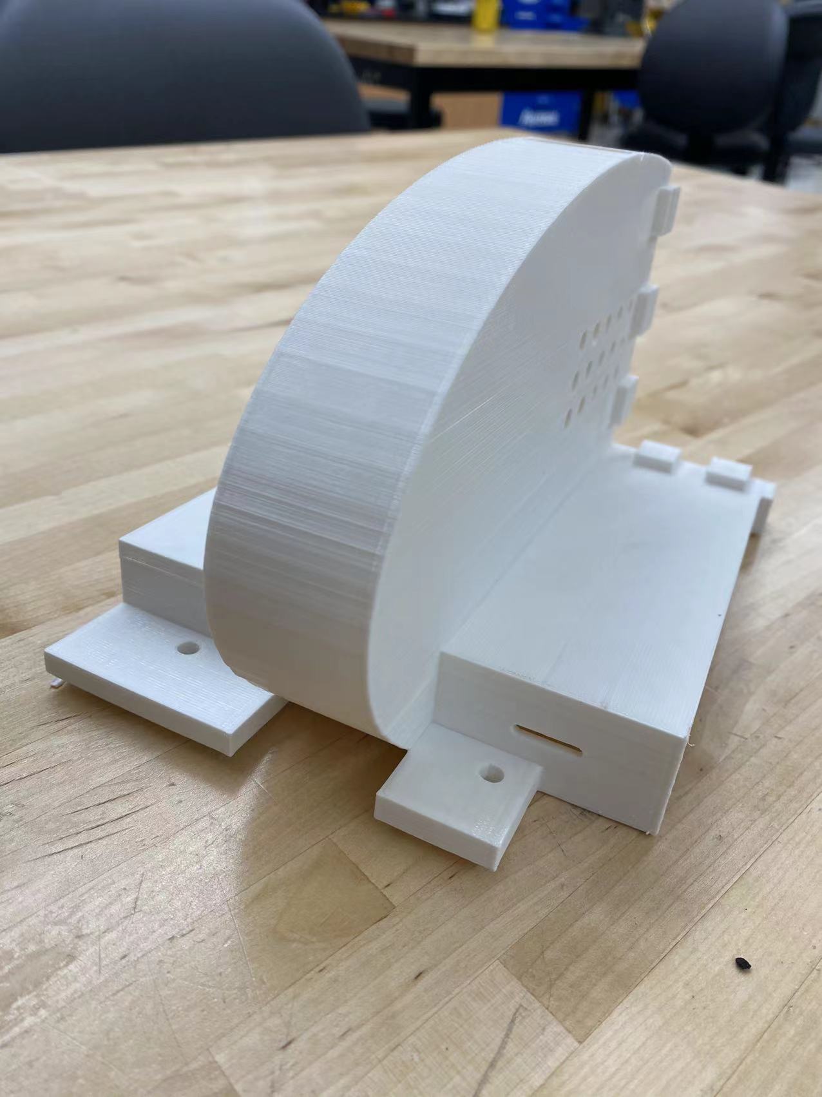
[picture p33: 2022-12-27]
Gen 1 3D print/airbladeinlet.jpg

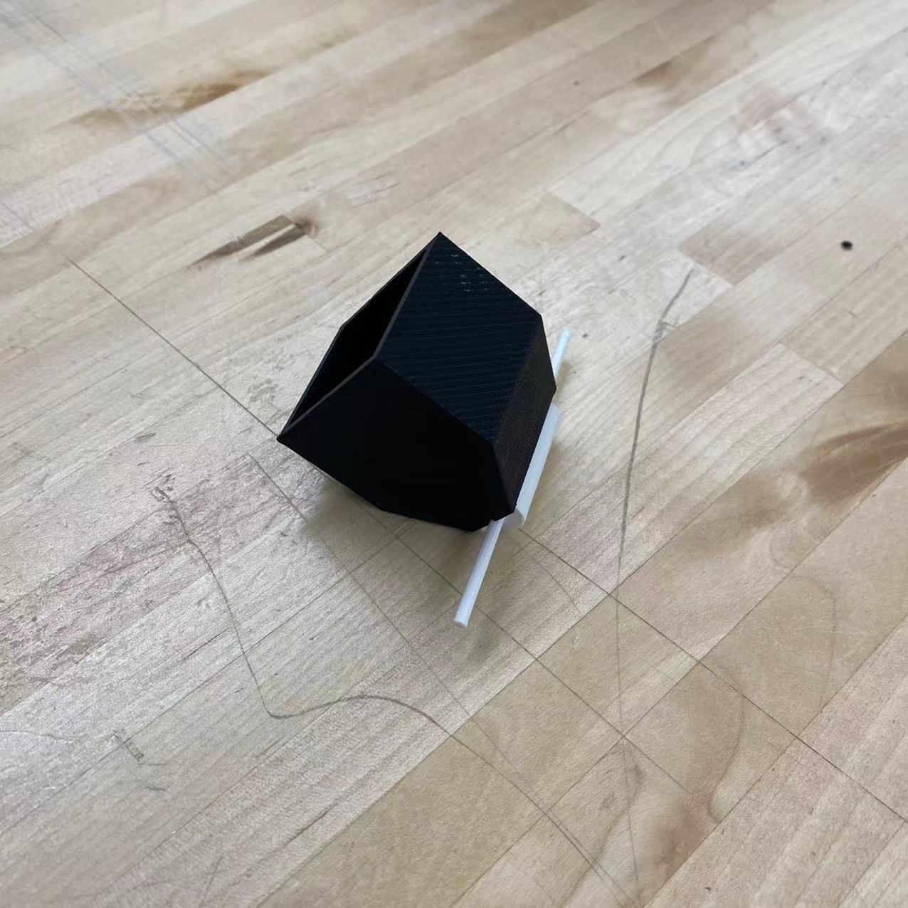
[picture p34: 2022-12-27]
Gen 1 3D print/hopper_gumball.jpg

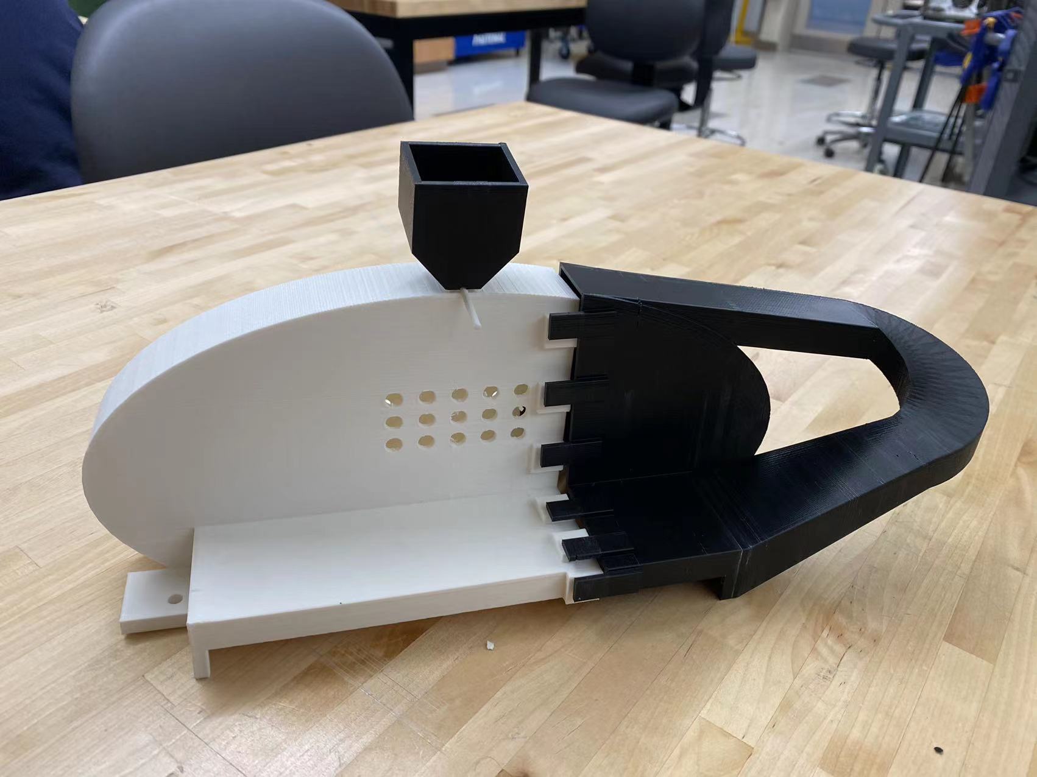
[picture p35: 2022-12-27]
Gen 1 3D print/glitterboxentire.jpg

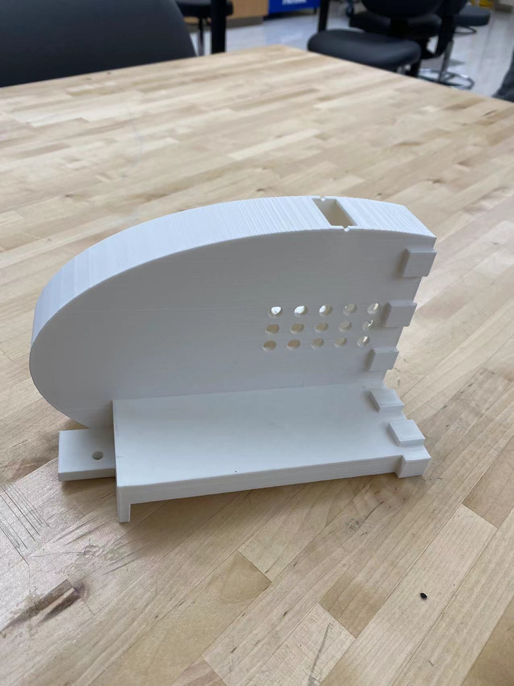
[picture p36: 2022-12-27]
Gen 1 3D print/othersideofbox.jpg

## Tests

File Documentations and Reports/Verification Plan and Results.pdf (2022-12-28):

# Verification Plan and Results

_____________________________________________________________________________________

ME186 / EE188 / BME 188 – Capstone II

Team 16 – Zen of the Art and Glitter Deposition
Anthony Vieriu
Emma Marston
Jake Varakian
Helen Wang
Date | Revision | Release Notes
1/24/2022 | 01 | Preliminary Draft
2/14/2022 | 02 | Resolved formatting errors, clarifying steps and processes
4/24/2022 | 03 | Final Draft

### Verification Plan and Results

Project 16 | 2

## Contents

### 1 Verification Plan Introduction

The Glitter Box is a module intended as a proof of concept for additive manufacturing. The module is designed to have a substrate with an adhesive pattern enter via a conveyor belt and be completely coated with a powder dependent on the user’s needs. This is done by dropping a dusting of powder onto the adhesive as it enters and using an air blade to remove any excess that has not been adhered at the exit of the module.

This document contains the results of testing all engineering specifications based on the Client’s (Integrity Industrial Inkjet Integration) expressed requirements for a successful product. Passing each ID listed in the document below should indicate a finished and fully functional product.

### 2 ID # 10 - Demonstration

### 2.1 Specification

The hopper shall deposit 1 tsp +/- 1/6 tsp of glitter per coating to prevent material waste.

### 2.2 Verification Approach

This specification will verify that material use remains efficient. This will be done by comparing the volume of glitter deposited for a single cycle to the volume of a teaspoon.

### 2.3 Equipment Needed (if any)

- 1 Teaspoon measurement
- Glitter
- Deposition Assembly
- Hopper
- Deposition roller

### 2.4 Procedure 2.4.1 Safety Considerations

- Potential hazard from airborne glitter
- Wear safety goggles during setup and demonstration
- Utilize an enclosed testing area

### 2.4.2 Setup

- Clean hopper of any residual glitter from past testing
- Place hopper assembly inside of enclosed testing area
- Deposit 1 Teaspoon of glitter into the hopper

### 2.4.3 Demonstration Procedure

- Deposit 1 cycles worth of glitter from the hopper by spinning the deposition cylinder ½ revolution
- Inspect glitter remaining in hopper to verify if any remains

### 2.5 Pass Criteria

The specification will pass If any amount of glitter remains in the hopper after deposition. This indicates that less than 1 tsp was deposited.

### 2.6 Results – 4/4/22 - Pass

This tested showed that an amount of glitter remains in the hopper after the half revolution. This indicates a pass.

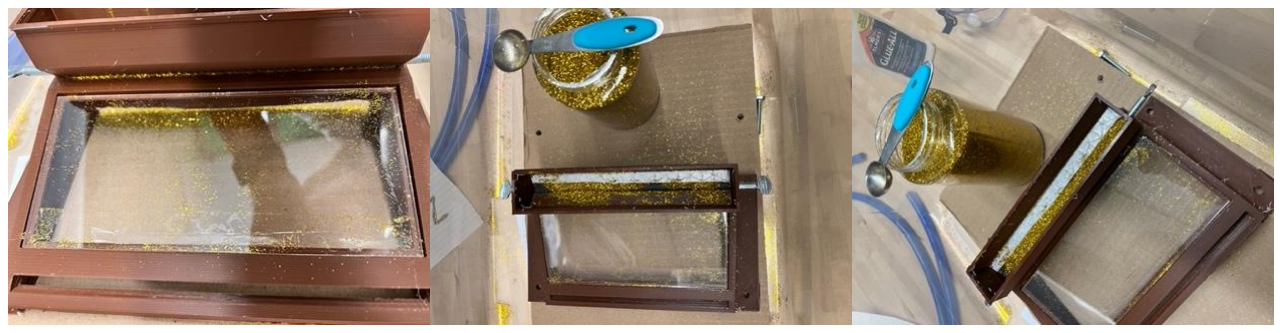
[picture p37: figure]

Figure 1 – Results showing glitter remaining in hopper.

### 3 ID # 20 - Test

### 3.1 Specification

The quantity of adhesive removed from the substrate shall not be below a 4 on the designated adhesive visual scale.

### 3.2 Verification Approach

This test will verify that the method for removing glitter does not also remove/distort the adhesive. This will be done by running the system with only adhesive and comparing the amount of displaced adhesive to the pre-determined visual scale. Passing this verification ensures high image quality and resolution for the print after exiting the module.

### 3.3 Equipment Needed

- Air Pump
- Air Blade Adaptor
- AC Power Socket
- Glitter Module
- Elmer’s Glue
- Small brush
- Substrate (for the results given here, a sheet of paper was used)
- ¼ 20” thumbscrews
- string

### 3.4 Procedure 3.4.1 Safety Considerations

- Safety goggles should be always worn during testing
- Testing should be performed inside of an isolated testing container

- Long hair should be tied up and loose jewelry should be removed and kept clear of the air pump inlet

### 3.4.2 Setup

- Secure the module inside of the isolated testing container on a flat surface using the thumbscrews
- Plug in the air pump and attach the air blade adaptor to the end of the tubing
- Affix the free side of the adaptor to the air blade inlet on the glitter module
- Using the small brush and the Elmer’s Glue, paint a design onto the substrate (Note: this design should remain constant for all testing to maintain a consistent reference)
- Attach the string to one end of substrate
- Place the substrate with the glue design slightly outside the entrance of module
- Feed the loose end of the string through the module so that the substrate may be pulled through
- Prepare video recording from above the module for future reference

### 3.4.3 Test Procedure

1. Take a picture of the Glue design on the substrate
2. Start recording from above the module
3. Turn on the air pump
4. Draw the substrate through the module at a constant speed by pulling on the loose end of the string
5. Once the glue has cleared the module, turn off the air pump
6. Take a final picture of the glue design
7. Compare the two photos of the glue design from before and after going through the module
8. Score the test from 0-5 on the adhesive visual scale, 0 being complete removal/distortion of all adhesive from the substrate and 5 being no adhesive removal/distortion.

### 3.5 Pass Criteria

To pass this specification the system must score a 4 or higher on the scale provided.

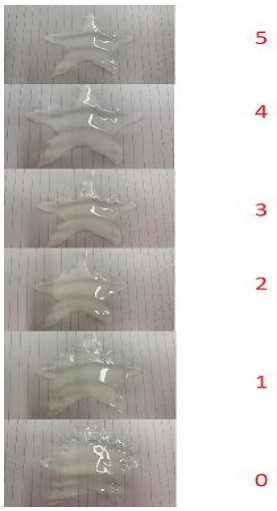
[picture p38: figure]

Figure 2 – Adhesive visual scale showing different levels of adhesive being disturbed on the substrate

### 3.6 Results – 4/18/22 - Pass

The demonstration resulted in a pass, where no adhesive was disturbed when air flow was applied within the system. A visual of the adhesive before and after shows no disruption to the substrate.

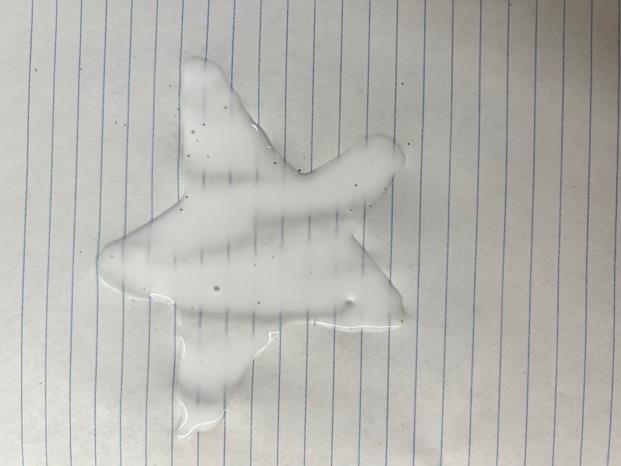
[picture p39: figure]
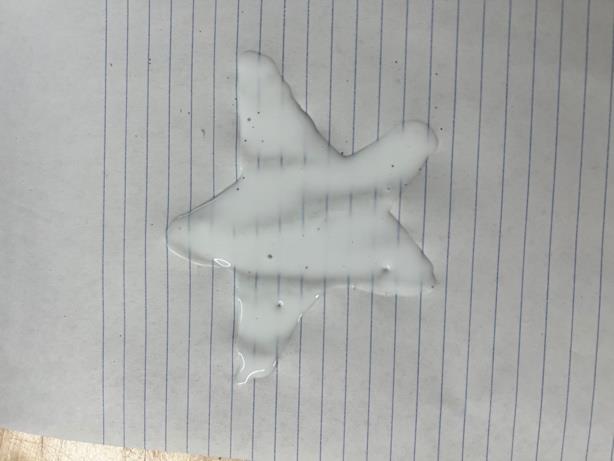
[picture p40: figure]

Figure 3: Before applied air flow | Figure 4: After applied air flow

### 4 ID # 30 - Demonstration

### 4.1 Specification

Box shall be compatible with ¼ 20-inch mounting threaded bolt holes on Integrity’s conveyor system.

### 4.2 Verification Approach

This analysis will verify that ¼ 20-inch bolts will fit into the mounting holes on the box, along with verifying that the mounting holes on the box line up with the mounting bolt holes on Integrity’s conveyor. To confirm this, ¼ 20-inch bolts will be used to test the size of the mounting holes while mounting the box onto a simulated conveyor with correct hole spacing based on CAD files provided by the client to test fitment.

### 4.3 Equipment Needed

- 4 ¼ 20-inch bolts and nuts
- Simulated conveyor with two rows 8.5 inches apart of mounting holes linearly spaced 1.5 inches apart.
- Coating box with mounting holes

### 4.4 Procedure 4.4.1 Safety Considerations

- Potential hazards from mechanical fastening
- Keep hands clear from pinch points
- Tie back or remove, necklaces, long hair, strings, sleeves, ETC.

### 4.4.2 Setup

- Align Mounting holes on box with mounting holes on simulated conveyor
- Prepare ¼ 20-inch bolts nearby for mounting

### 4.4.3 Demonstration Procedure

- Begin to screw in the ¼ 20-inch bolts into the box mounting holes through the simulated conveyor mounting holes
- Secure bolts using wing-nuts until box is firmly positioned on simulated conveyor
- Inspect the bolt/box/conveyor assembly to ensure the box is locked in place and fits properly

### 4.5 Pass Criteria

The specification will pass if the mounting holes on the box line up with the holes on the simulated conveyor allowing all the bolts to screw in and lock the box in place on top of the conveyor.

### 4.6 Results – 4/4/22 - Pass

These results show that the ¼ 20-inch bolts fit directly into the mounting holes designed to fit these ¼ 20-inch bolts. These results also show that the mounting holes on the box line up with the mounting holes on Integrity’s conveyor. Once the bolts are in place, the box is securely mounted and will not move even if accidentally nudged. This means that ID 70 passes the verification check.

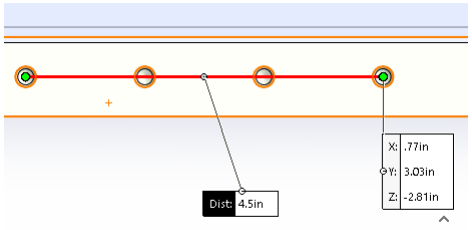
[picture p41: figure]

Figure 5 – Solidwork file showing exact dimentions of Integrity’s conveyor

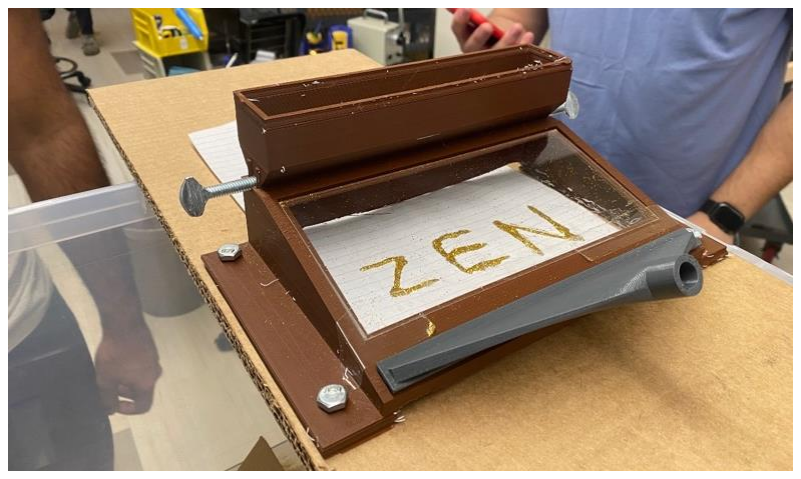
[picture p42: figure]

Figure 6 – Coating chamber mounted onto makeshift conveyor with ¼ 20 inch bolts.

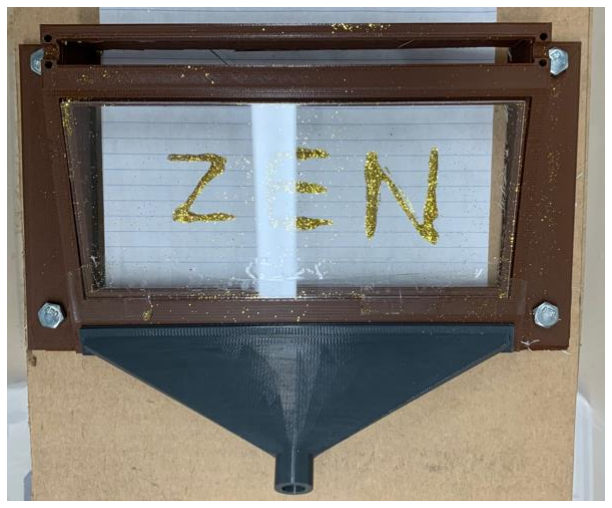
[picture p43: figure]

Figure 7 – Clear view of all the bolts fastened down, holding in the coating chamber.

### 5 ID # 40 - Demonstration

### 5.1 Specification

Glitter coating process shall be haltable within 3 seconds after command is initiated.

### 5.2 Verification Approach

The purpose of this verification is to show that, in an emergency, the coating process may be rapidly halted to prevent the aerosolization of powder. This will be done by timing how long it takes to completely halt air flow into the module.

### 5.3 Equipment Needed

- 3D printed prototype
- Particles/Glitter
- Air pump
- Air blade adaptor
- Timer/stopwatch
- Substrate (Paper was used for results shown below)
- Testing container
- ¼ - 20 in screws
- string

### 5.4 Procedure 5.4.1 Safety Considerations

- Remove or isolate the battery before or after working to prevent shock hazards.
- Air Pump
- High pressure system, release air slowly to not create a mess of airborne particles
- Wear safety goggles during testing to prevent glitter flying into eyes.
- Use testing container to control glitter escape

### 5.4.2 Setup

- Ensure the bottom of the testing area is glitter-free and clean
- Place adhesive (Elmer’s glue) onto the substrate
- Attach one end of the string to the substrate and pull the loose end through the box so that it may be drawn through the module
- Position the glitter box above the substrate
- Fill hopper with glitter
- Attach air blade adaptor to air pump tubing and affix the loose end to the air blade inlet in the glitter module

- Plug in air pump

### 5.4.3 Demonstration Procedure

- Turn on the air inflator.
- Deposit the 1 tsp of glitter into the glitter box using the hopper by rotating the roller.
- Begin drawing the substrate through the module at a constant speed by pulling on the loose end of the string
- Start timer and turn off the inflator by using the pressure control valve on the air pump tubing simultaneously.
- Once glitter is motionless within system, stop the timer
- Record time to stop
- Unplug the inflator

### 5.5 Pass Criteria

To pass the test, the glitter must halt dispersion within 3 seconds of issue the command to stop the inflator from distributing air. If the timer results in more than 3 seconds, then the verification has failed. To verify the time it takes to halt the air flow, a video is taken as well to record the exact length of the process.

### 5.6 Results – 4/4/22 – 1:00PM – Pass

The demonstration passed the criteria of halting air flow within 3 seconds of initiating the action. Below in Figure 8 is a frame of the video displaying our prototype in action, as well as the user halting the air flow. The time it took to stop was 2 seconds, less than the 3 seconds required to pass this verification.

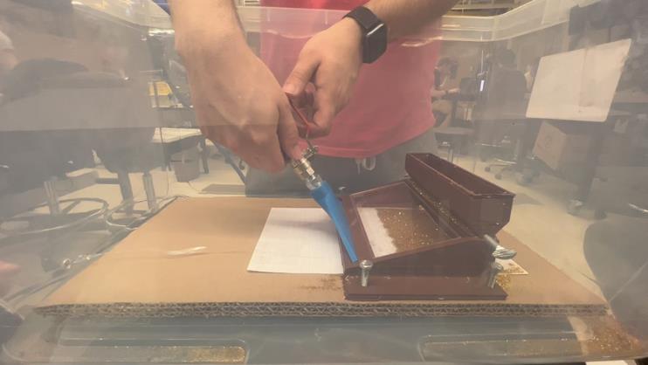
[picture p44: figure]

Figure 8 – User Halting Air Flow: 2.21 seconds

### 6 ID # 50 - Test

### 6.1 Specification

Box shall be able to continuously displace glitter for 1 minute.

### 6.2 Verification Approach

The purpose of this verification is to show that the module can function continuously for multiple coatings over a longer period. This will be done by running the system continuously for 1 minute and documenting any failures.

### 6.3 Equipment Needed

- Air pump
- Air blade adapter
- AC power socket
- Glitter Module
- Glitter
- Isolated testing container
- Substrate (for the results given here, a sheet of paper was used)
- ¼ 20” thumbscrews
- String

### 6.4 Procedure 6.4.1 Safety Considerations

- Safety goggles should be always worn during testing
- Testing should be performed inside of an isolated testing container
- Long hair should be tied up and loose jewelry should be removed and kept clear of the air pump inlet

### 6.4.2 Setup

- Secure the module inside of the isolated testing container on a flat surface using the thumbscrews
- Plug in the air pump and attach the air blade adaptor to the end of the tubing
- Affix the free side of the adaptor to the air blade inlet on the glitter module
- Attach the string to one end of the substrate
- Place the substrate slightly outside the entrance of module
- Feed the loose end of the string through the module so that the substrate may be pulled through
- Load the hopper with glitter
- Prepare video recording from above the module for future reference

### 6.4.3 Test Procedure

- Start recording from above the module
- Turn on air pump
- Slowly draw the substrate through the module at a constant speed by pulling on the loose end of the string
- Take note of any errors that occur during the minute (glitter escape, hopper jamming, etc.)
- After 1 minute has elapsed turn of the pump and halt the substrate

### 6.5 Pass Criteria

To pass this verification, the module should be able to function continuously for 1 minute with no errors arising.

### 6.6 Results – 4/6/22 - Pass

The result from the test showed that the glitter box surpassed the 1 minute timer test, with the inflator running continuously. No fractures occurred and minimal glitter escaped, allowing the specification to pass.

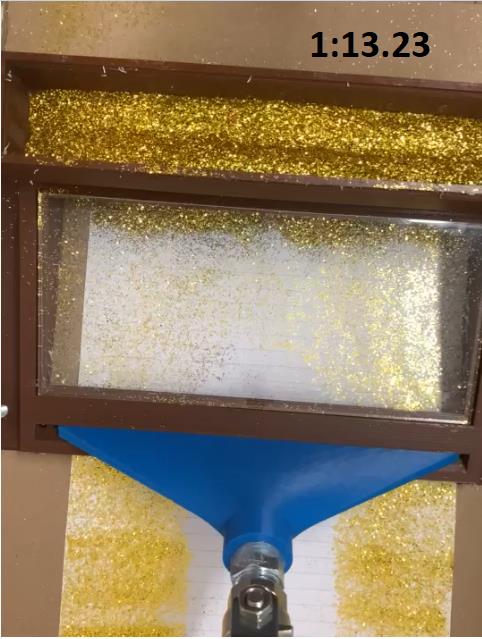
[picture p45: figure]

Figure 9 – Coating machine will run for over one minute

### 7 ID # 60 - Demonstration

### 7.1 Specification

The chamber length shall be less than 7 inches

### 7.2 Verification Approach

The purpose of this verification is to show that the module does not take up too much space on the testing conveyor belt in the client’s lab. This will be done by measuring the chamber length of the design using a ruler and comparing to the client’s prescribed length in inches.

### 7.3 Equipment Needed

- Metric ruler
- Glitter module

### 7.4 Procedure

This verification procedure is relatively simple. The length of the chamber shall be measured by a metric ruler.

### 7.4.1 Safety Considerations

- Take note of pinch points between the edge of the module and the ruler

### 7.4.2 Setup

- Place the module on a clean flat surface
- Prepare a ruler with inch measurements

### 7.4.3 Demonstration Procedure

- Place the ruler along the side edge of the module and record the length in inches

### 7.5 Pass Criteria

If the measurement of module length is less than 7 inches, than it passes the verification.

### 7.6 Results – 4/6/22 - Pass

The final box design is 5.5 inches long after measurements, so the testing results pass the criteria.

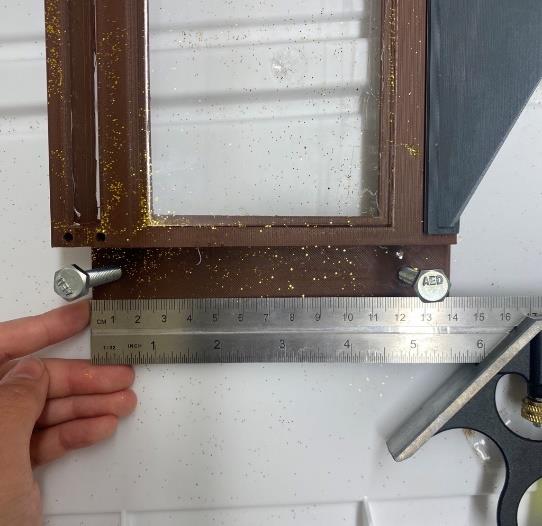
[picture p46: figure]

Figure 10 - Chamber Size Measurement: 5.5 inches

### 8 ID # 70 - Demonstration

### 8.1 Specification

The box shall have at least 1 side that can be seen through to visualize glitter flow/adhesion.

### 8.2 Verification Approach

This inspection will verify that the 3D printed prototype has a specific area that is transparent, so the user is able to view what is occurring inside the chamber. This will be verified in the

SolidWorks model as well as the printing specifications to ensure the material that is being printed is transparent.

### 8.3 Equipment Needed

- 3D printed prototype
- Laser cut 8mm thick acrylic piece for 3.5 x 7.5inch

### 8.4 Procedure 8.4.1 Safety Considerations

- When installing the transparent wall, be mindful of pinch points

### 8.4.2 Setup

- Prepare the glitter module on a flat surface
- Have the laser cut transparent piece ready

### 8.4.3 Demonstration Procedure

- Place the laser cut piece in the indented portion on the top side of the box
- Verify that there are no gaps, and the interior of the module may be seen through the sheet

### 8.5 Pass Criteria

To pass inspection, at least one side of the exterior of the prototype is transparent enough to clearly showcase the coating of the adhesive inside which will be visually apparent.

### 8.6 Results – 3/1/2022- Pass

The results from the inspection conclude that one side of the exterior is transparent and showcases the particle flow/particle adhesion, passing the specification. See figure below to view the results of transparent wall.


Figure 11 – View of box interior through transparent top

### 9 ID # 80 - Test

### 9.1 Specification

The quantity of escaped glitter shall not exceed a 2 on the designated glitter density visual scale.

### 9.2 Verification Approach

This test will verify that glitter entering the system is not blown out of the module into the surrounding area. This will be done by running the system as intended and using a visual scale to score the amount of escaped glitter based on an acceptable range.

### 9.3 Equipment Needed

- Air Pump
- Air Blade Adaptor
- AC Power Socket
- Glitter Module
- Elmer’s Glue
- Glitter
- Small brush
- Substrate (for the results given here, a sheet of paper was used)
- ¼ 20” thumbscrews
- String

### 9.4 Procedure 9.4.1 Safety Considerations

- Safety goggles should be always worn during testing
- Testing should be performed inside of an isolated testing container
- Long hair should be tied up and loose jewelry should be removed and kept clear of the air pump inlet

### 9.4.2 Setup

- Secure the module inside of the isolated testing container on a flat surface using the thumbscrews
- Plug in the air pump and attach the air blade adaptor to the end of the tubing
- Affix the free side of the adaptor to the air blade inlet on the glitter module
- Using the small brush and the Elmer’s Glue, paint a design onto the substrate (Note: this design should remain constant for all testing to maintain a consistent reference)
- Attach the string to one end of substrate
- Place the substrate with the glue design slightly outside the entrance of module
- Feed the loose end of the string through the module so that the substrate may be pulled through
- Deposit 1 tsp of glitter into the hopper
- Clean any glitter remaining in testing container from previous trials
- Prepare video recording from above the module for future reference

### 9.4.3 Test Procedure

1. Start recording from above the module
2. Turn on the air pump

3. Begin drawing the substrate through the chamber
4. As the substrate is about to reach the glitter entrance, slowly rotate the deposition cylinder ½ revolution
5. Continue drawing the substrate through the chamber until the glue design has cleared the module
6. Turn of the air pump
7. Take a picture of the testing container and take note of any escaped glitter
8. Score the test from 0-5 using the glitter density visual scale, 0 being no escaped glitter and 5 being complete glitter escape.

### 9.5 Pass Criteria

To pass this specification the system must score a 2 or lower, as seen in Figure 12.


Figure 12 – Visual scale for the amount of glitter left behind by the air knife pass.

### 9.6 Results – 4/18/22 - Fail

After following procedure for this ID specification, the test resulted in a fail due to glitter escaping the rear of the device. The air flow was too strongly applied and forced glitter out of the back inlet.

### 10 ID # 90 - Demonstration

### 10.1 Specification

Shall not have any contact between any pieces of metal or electrical wires within the module that can create heat, sparks, or shavings.

### 10.2 Verification Approach

This Demonstration will verify that there is not any contact between any pieces of metal or electrical wires within the module that can create heat, sparks, or shaving. To demonstrate that there will be no risk of creating heat, sparks, or shavings within the box, the unit will be disassembled to show that there are no electrical wires on the inside of the chamber and that there are no metal pieces that will be touching each other or capable of causing any of the previously listed problems within the chamber.

### 10.3 Equipment Needed

- Coating chamber assembly

### 10.4 Procedure

Disassemble the coating chamber assembly to show that there are no risks of electrical wires or metal on metal contact that can cause heat, sparks, or shavings within the chamber.

### 10.5 Pass Criteria

In order to pass this demonstration, it should be clear that no contact between any pieces of metal or electrical wires within the module that would create heat, sparks, or shavings are present within the module.

### 10.6 Results – 4/4/2022 - Pass

There are currently no contact points between metal that touch one another or could create shavings and no wires present in the design, so the result passes the criteria.


Figure 13 – Visual of no wires or metal contact within the chamber

### 11 ID # 100 - Test

### 11.1 Specification

The quantity of adhered glitter coating the substrate shall not be below a 4 on the designated glitter density visual scale.

### 11.2 Verification Approach

This test will verify that the method for removing glitter does not also remove the glitter that has landed on the adhesive. This will be done by running the system with wet glue that has been pre-coated with glitter and comparing the number of displaced particles to the pre-determined visual scale. Passing this verification ensures high image quality and resolution for the product after exiting the module.

### 11.3 Equipment Needed

- Air Pump
- Air blade adaptor
- AC power plug and socket
- Glitter module
- Elmer’s glue
- Glitter

### 11.4 Procedure 11.4.1 Safety Considerations

- Wear safety goggles during testing
- Testing should take place inside of an isolated testing container
- Glitter particles may be airborne if the flow settings are too high.

### 11.4.2 Setup

- Secure the module inside of the isolated testing container on a flat surface
- Plug in the air pump and attach the air blade adaptor to the end of the tubing
- Affix the free side of the adaptor to the air blade inlet on the glitter module
- Place a design with wet glue fully coated with glitter at conveyor inlet
- Prepare video recording from above the module for future reference

### 11.4.3 Test Procedure

- Line up wet glue with glitter onto conveyor inlet and start recording
- Turn on air pump and begin to pull through the conveyor without depositing glitter
- As pulling through the conveyor, examine for glitter particles falling off the adhesive
- Compare images of before and after running through the system with the designated glitter density visual scale

### 11.5 Pass Criteria

To pass the test, the glitter shall not be below a 4 on the designated glitter visual scale after passing through the system.


Figure 14 – Glitter visual scale

### 11.6 Pass – 4/19/2022

This test scored a 4 on the coating scale above, while there is still a miniscule amount of visual adhesive, the design is essentially entirely coated. This specification passes the verification check.


Figure 15 – Test Results for ID 100

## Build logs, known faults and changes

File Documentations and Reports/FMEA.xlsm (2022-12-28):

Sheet: Cover Page
Project 16 - Zen and The Art of Glitter Deposition
Failure Modes Effects Analysis - Glitter Module
 |  | Team Member #1 | Jake Varakian
 |  | Team Member #2 | Helen Wang
 |  | Team Member #3 | Emma Marston
 |  | Team Member #4 | Anthony Vieriu
Revision History
 | Revision | Date | Description of Change
 | 1 | 2022-02-25 | First Release

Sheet: Ground Rules
Bounds of FMEA
Parts evaluated- Air Inlet (source and nozzle), Roller, Hopper
Parts and system manufactured/assembled as designed
Effects of failure are evaluated at user level
Inputs/specification limits are correct and reflect design needs
Design Use Profile
Operated by conveyor technician, no user error
Will be operated with a variety of powders
Will be operated indoors in a manufacturing facility
Will be running ~12 hours per day
Regular inspections will be performed
Module will be cleaned prior to use
Quantity in use
Assume 200 modules in use
Other
none

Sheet: Scales
Rating for Severity
Rating | Effect of Failure Mode | Criteria
10 | Extreme | Major damage caused to other assembly line components resulting in injury of conveyor technician
9 | Severe | Major damage to other assembly line components, no harm to technician
7 | High | Destruction of module and/or halting of assembly line.
5 | Moderate | System failure resulting in material escaping the module, delay of assembly line
3 | Minimal | Slight powder build-up as part of typical use
1 | No Effect | No hazards present, module operates as intended
Rating for Occurrence
Rating | Likelihood of Occurrence | Criteria
10 | Almost Certain | Design will not prevent root cause from occuring. >1 per year of operation
9 | Very High Chance | Deisgn will not prevent root cause from occurring. 1/ module lifetime or 100% chance for each module in operation
7 | High Chance | Low confidence the design will prevent root cause from occurring. 1/10 module lifetimes or 10% chance on every module in operation
5 | Moderate Chance | Moderate confidence design will precent root cause. 1/100 module lifetimes or 1% chance on every module in operation.
3 | Low Chance | extremely confident design will prevent root cause. 1/1,000 module lifetimes of 0.1% chance on every module in operation
1 | Almost Uncertain | Design will prevent root cause from occuring 100% of the time.
Rating for Detection
Rating | Likelihood of Detection | Criteria
10 | Almost Uncertain | Failure impossible to detect with all detection controls.
9 | Low Chance | No targeted design detection controls.
8 |  | Failure unlikely to be detected with in-service detection controls.
7 | Moderate Chance | No targeted design detection controls.
6 |  | Failure may be detected with in-service detection controls.
5 | High Chance | Failure may be detected with design detection controls that target the failure mode.
4
3 | Very High Chance | Failure is likely to be detected with design detection controls that target the failure mode.
2
1 | Almost Certain | Failure is certain to be detected with design detection controls that target the failure mode.

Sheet: FMEA - Form
FMEA Title | Glitter Module
1 - Item | 2 - Item Function(s) | 3 - Functional Failure Mode(s) | 4 - Potential Effect(s) of Failure | 5 - S e v | 6 - Root cause(s) of Failure | 7 - Current Prevention Control(s) (prevention of root cause) | 8 - O c c | 9 - Current Detection Controls (detection of root cause) | 10 - D e t | R P N | 12 - Recommended Action(s) | 12 - Person Responsible and Target Completion Date | 12 - Rescore when Action has been taken.
 |  |  |  |  |  |  |  |  |  |  |  |  | Actions Taken | S | O | D | RPN
Roller | transfer glitter from hopper into the chamber | Over deposition of glitter | far too much material being inserted causing expensive waste. too much material may be unable to adequately mix | 5 | Deposition dimples are too big | Compared volumes to client specified values | 3 | Transparent walls to observe addition of glitter during testing | 5 | 75 | adjust dimple size | Jake Varakian 3/09 |  | 1 | 1 | 5 | 5
 |  |  |  | 5 | Gaps between roller and hopper are too big | Incorporated "sheath" around roller to seal gaps | 3 | Transparent walls to observe addition of glitter during testing | 5 | 75 | Tighten tolerances | Anthony Vieriu 03/09 |  | 3 | 1 | 5 | 15
 |  | Clumping of glitter during transfer | Could jam roller. Prevent mixing, resulting in inaddequate coating of product | 7 | Deposition dimples are too big | Compared volumes to client specified values | 3 | Transparent walls to observe addition of glitter during testing | 5 | 105 | adjust dimple size | Emma Martson 3/09 |  | 1 | 1 | 5 | 5
 |  |  |  | 5 | Gaps between roller and hopper are too big | Incorporated "sheath" around roller to seal gaps | 3 | Transparent walls to observe addition of glitter during testing | 5 | 75 | Tighten tolerances | Anthony Vieriu 03/09 |  | 3 | 1 | 5 | 15
 |  |  |  | 5 | Particles loaded into hopper are already clumped | none | 5 | Transparent walls to observe addition of glitter during testing | 5 | 125 | Look into addition of mesh or sieve into hopper | Emma Martson 4/1 |  | 1 | 3 | 5 | 15
 |  | Under deposition of glitter | Inaddequate coating | 5 | Deposition dimples are too small | Compared volumes to client specified values | 3 | Transparent walls to observe addition of glitter during testing | 3 | 45 | adjust dimple size | Emma Martson 3/9 |  | 1 | 1 | 5 | 5
Hopper | To hold glitter for future depostion via the roller | Hopper doesn’t guide glitter to roller | No material gets added to the chamber. Inaddequate coating. | 5 | Invalid hopper geometry | Adjust the geometry of the interior of the hopper | 3 | Visual detection of glitter escaping exterior of hopper | 5 | 75 | Adjust the geometry of the interior of the hopper | Emma Martson 3/9 |  | 1 | 1 | 5 | 5
 |  |  |  | 3 | Tolerance issues | Tolerance of 3D printer is taken into account during 3D modeling | 9 | Visual assesment of hopper fit | 5 | 135 | Alter tolerances | Anthony Vieriu 03/09 |  | 1 | 1 | 5 | 5
 |  | Glitter escapes hopper not in the intended manner | Glitter/powder escapes into the manufacturing location. Expensive material waste. Potential damage to other machinery and possible injury to conveyor technician. | 10 | Hopper isnt properly sealed | tape to seal edges/connection points. Top of hopper is currently open to room | 10 | Visual assesment of glitter leakage into testing environment | 5 | 500 | look into other sealing options (glue gun, mechanical attachment, etc.) | Helen Wang 3/9 | Used tape as a wall to seal the box as leakage fix | 5 | 5 | 5 | 125
 |  |  |  | 9 | Hopper is overfilled | none | 1 | Visual assesment of glitter reloading into hopper | 3 | 27 | add fill line/limit to hopper to inidicate max load | Anthony Vieriu 03/09 |  | 9 | 1 | 1 | 9
Air Inlet (source and nozzle) | To promote mixing of glitter to coat adhesive inside chamber | Air source is too powerful | Could blow glitter out of the chamber. Could cause hopper blowout. Could disturb adhesive. | 10 | Air source settings are not adequate for this application | have tried several air sources to find a good fit | 3 | Visual assesment of glitter escaping chamber as well as adhesive pattern deformation. | 3 | 90 | Try variable air sources and settings | Helen Wang 2/23 |  | 9 | 3 | 1 | 27
 |  |  |  | 10 | Nozzle accelerates flow too much (nozzle too small) | Have tried several nozzles to find a good fit | 5 | Visual assesment of glitter escaping chamber as well as adhesive pattern deformation. | 3 | 150 | continue testing nozzles to optimize flow | Jake Varakian 2/22 | Designed Air Blade adaptor for current nozzle | 9 | 3 | 3 | 81
 |  | Air source too weak | Inaddequate coating. Unable to circulate glitter. Unable to contain glitter within box. | 7 | Air source settings are not adequate for this application | have tried several air sources to find a good fit | 7 | Transparent walls to observe glitter circulation and coating of adhesive inside chamber. | 5 | 245 | Try variable air sources and settings | Helen Wang 2/23 |  | 5 | 5 | 5 | 125
 |  |  |  | 7 | Nozzle does not accelerates flow enough (nozzle too big) | Have tried several nozzles to find a good fit | 5 | Transparent walls to observe glitter circulation and coating of adhesive inside chamber. | 5 | 175 | continue testing nozzles to optimize flow such as air blade adaptor for nozzle | Jake Varakian 2/22 | Designed Air Blade adaptor for current nozzle | 5 | 3 | 5 | 75
 | Contain glitter in chamber for reuse | Air source is too powerful | Could blow glitter out of the chamber or hopper. Could disturb adhesive | 7 | Air source settings are not adequate for this application | Have tried several air sources to find a good fit | 7 | Transparent walls to observe glitter circulation and coating of adhesive inside chamber. | 5 | 245 | continue testing variable air sources and settings | Emma Martson 2/23 | Tested variable air sources and settings | 5 | 5 | 5 | 125
 |  |  |  | 7 | Nozzle accelerates flow too much (nozzle too small) | Have tried several nozzles to find a good fit | 5 | Transparent walls to observe glitter circulation and coating of adhesive inside chamber. | 5 | 175 | Continue testing new nozzle designs such as air blade adaptor for nozzle | Jake Varakian 2/22 | Designed Air Blade adaptor for current nozzle | 5 | 3 | 5 | 75
 |  | Air source too weak | Unable to contain glitter in chamber | 7 | Air source settings are not adequate for this application | have tried several air sources to find a good fit | 7 | Transparent walls to observe glitter circulation and coating of adhesive inside chamber. | 5 | 245 | continue testing variable air sources and settings | Helen Wang 2/23 | Tested variable air sources and settings | 5 | 5 | 5 | 125
 |  |  |  | 7 | Nozzle does not accelerates flow enough (nozzle too big) | Have tried several nozzles to find a good fit | 5 | Transparent walls to observe glitter circulation and coating of adhesive inside chamber. | 5 | 175 | Continue testing new nozzle designs such as air blade adaptor for nozzle | Jake Varakian 2/22 | Designed Air Blade adaptor for current nozzle | 5 | 3 | 5 | 75
 |  |  |  |  |  |  |  |  |  | 0 |  |  |  |  |  |  | 0
 |  |  |  |  |  |  |  |  |  | 0 |  |  |  |  |  |  | 0
 |  |  |  |  |  |  |  |  |  | 0 |  |  |  |  |  |  | 0
 |  |  |  |  |  |  |  |  |  | 0 |  |  |  |  |  |  | 0
 |  |  |  |  |  |  |  |  |  | 0 |  |  |  |  |  |  | 0
 |  |  |  |  |  |  |  |  |  | 0 |  |  |  |  |  |  | 0
 |  |  |  |  |  |  |  |  |  | 0 |  |  |  |  |  |  | 0
 |  |  |  |  |  |  |  |  |  | 0 |  |  |  |  |  |  | 0
 |  |  |  |  |  |  |  |  |  | 0 |  |  |  |  |  |  | 0
 |  |  |  |  |  |  |  |  |  | 0 |  |  |  |  |  |  | 0
 |  |  |  |  |  |  |  |  |  | 0 |  |  |  |  |  |  | 0
 |  |  |  |  |  |  |  |  |  | 0 |  |  |  |  |  |  | 0
 |  |  |  |  |  |  |  |  |  | 0 |  |  |  |  |  |  | 0
 |  |  |  |  |  |  |  |  |  | 0 |  |  |  |  |  |  | 0
 |  |  |  |  |  |  |  |  |  | 0 |  |  |  |  |  |  | 0
 |  |  |  |  |  |  |  |  |  | 0 |  |  |  |  |  |  | 0
 |  |  |  |  |  |  |  |  |  | 0 |  |  |  |  |  |  | 0
 |  |  |  |  |  |  |  |  |  | 0 |  |  |  |  |  |  | 0
 |  |  |  |  |  |  |  |  |  | 0 |  |  |  |  |  |  | 0
 |  |  |  |  |  |  |  |  |  | 0 |  |  |  |  |  |  | 0
 |  |  |  |  |  |  |  |  |  | 0 |  |  |  |  |  |  | 0
 |  |  |  |  |  |  |  |  |  | 0 |  |  |  |  |  |  | 0
 |  |  |  |  |  |  |  |  |  | 0 |  |  |  |  |  |  | 0
 |  |  |  |  |  |  |  |  |  | 0 |  |  |  |  |  |  | 0
 |  |  |  |  |  |  |  |  |  | 0 |  |  |  |  |  |  | 0
 |  |  |  |  |  |  |  |  |  | 0 |  |  |  |  |  |  | 0
 |  |  |  |  |  |  |  |  |  | 0 |  |  |  |  |  |  | 0
 |  |  |  |  |  |  |  |  |  | 0 |  |  |  |  |  |  | 0
 |  |  |  |  |  |  |  |  |  | 0 |  |  |  |  |  |  | 0
 |  |  |  |  |  |  |  |  |  | 0 |  |  |  |  |  |  | 0
 |  |  |  |  |  |  |  |  |  | 0 |  |  |  |  |  |  | 0
 |  |  |  |  |  |  |  |  |  | 0 |  |  |  |  |  |  | 0
 |  |  |  |  |  |  |  |  |  | 0 |  |  |  |  |  |  | 0
 |  |  |  |  |  |  |  |  |  | 0 |  |  |  |  |  |  | 0
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
